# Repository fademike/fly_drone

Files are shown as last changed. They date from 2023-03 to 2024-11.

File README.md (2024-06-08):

# fly_drone

My example drone. (in development)

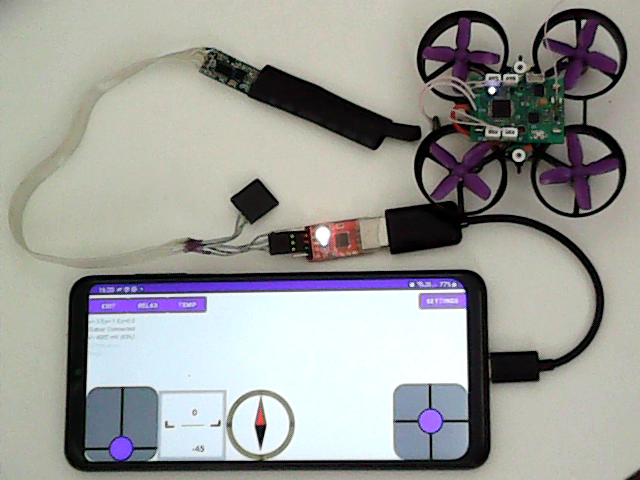
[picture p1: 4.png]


How to connect:
Android phone (AppFlyControl) <-> usb-uart(example: cp2102) <-> uart->rf (STM8S003_AND_SI4463) <-> fly_drone
<br>
or:
<br>
Android phone (QGroundControl or AppFlyControl) <-wifi-> Linux PC (flyLinuxServer) <-> uart->rf (STM8S003_AND_SI4463) <-> fly_drone

on board:
- DC-DC for 2,3,..S battery operation. To operate on a 1S battery, it is necessary to replace the components to turn off the DC-DC.
- RF SI4463 433MHz radio transceiver. when changing the frequency, you can to change components and programmatically set a different frequency.
- imu mpu6050
- 4pcs 3-pin connector for servo motor/ESC (IMP 1-2 ms) for 4pcs brushed motors need to set mosfet or esc for brushed motors.
- i2c connector, for example: for VL53L0X
- connector for debugging by swdio/uart

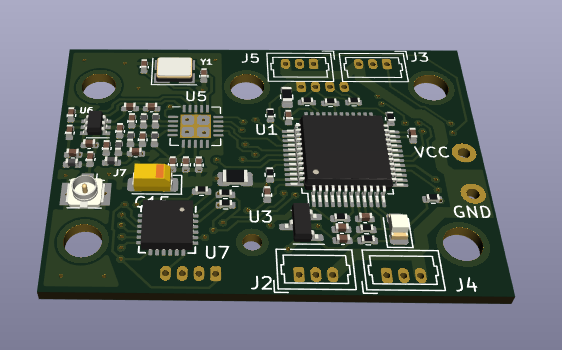
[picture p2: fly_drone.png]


For connect brushed motors with esc or servo motor, you can use convertor on attiny13a. example: kicad->tiny_2nmosfet.
For connect 4pcs brushed motors, you can use n-mosfet on every channel.

<br>
Code:
<br>
bootloader (update firmware via RF by FlyLinuxServer)<br>
fly_drone<br>
- mavlink protocol:<br>
-- params list settings(PID, mux chan, motor settings, orientation)<br>
-- RC_CHANNELS<br>
-- COMMAND_LONG - ARM_DISARM/CALIBRATION/REBOOT<br>
-- MSG_STATUSTEXT - logs<br>
- imu, rf, vl53l0x<br>
- acc and gyro calibrate<br>
- for save params and acc calibrate on flash, need to change "flash_params"<br>
- it is compatible with qgroungcontrol (tested on android)<br>
<br>
And in repository:<br>
kicad:<br>
- ESC_atmega8 - esc for brashless motor. (need to changed frequency by fuses)<br>
- stm32f103_Fly.. - fly_drone project<br>
- tiny_2nmosfet - esc for connection 4 brashed motors(independent 4 in, 4 out)<br>
<br>
video fly_drone.mpg in video repository

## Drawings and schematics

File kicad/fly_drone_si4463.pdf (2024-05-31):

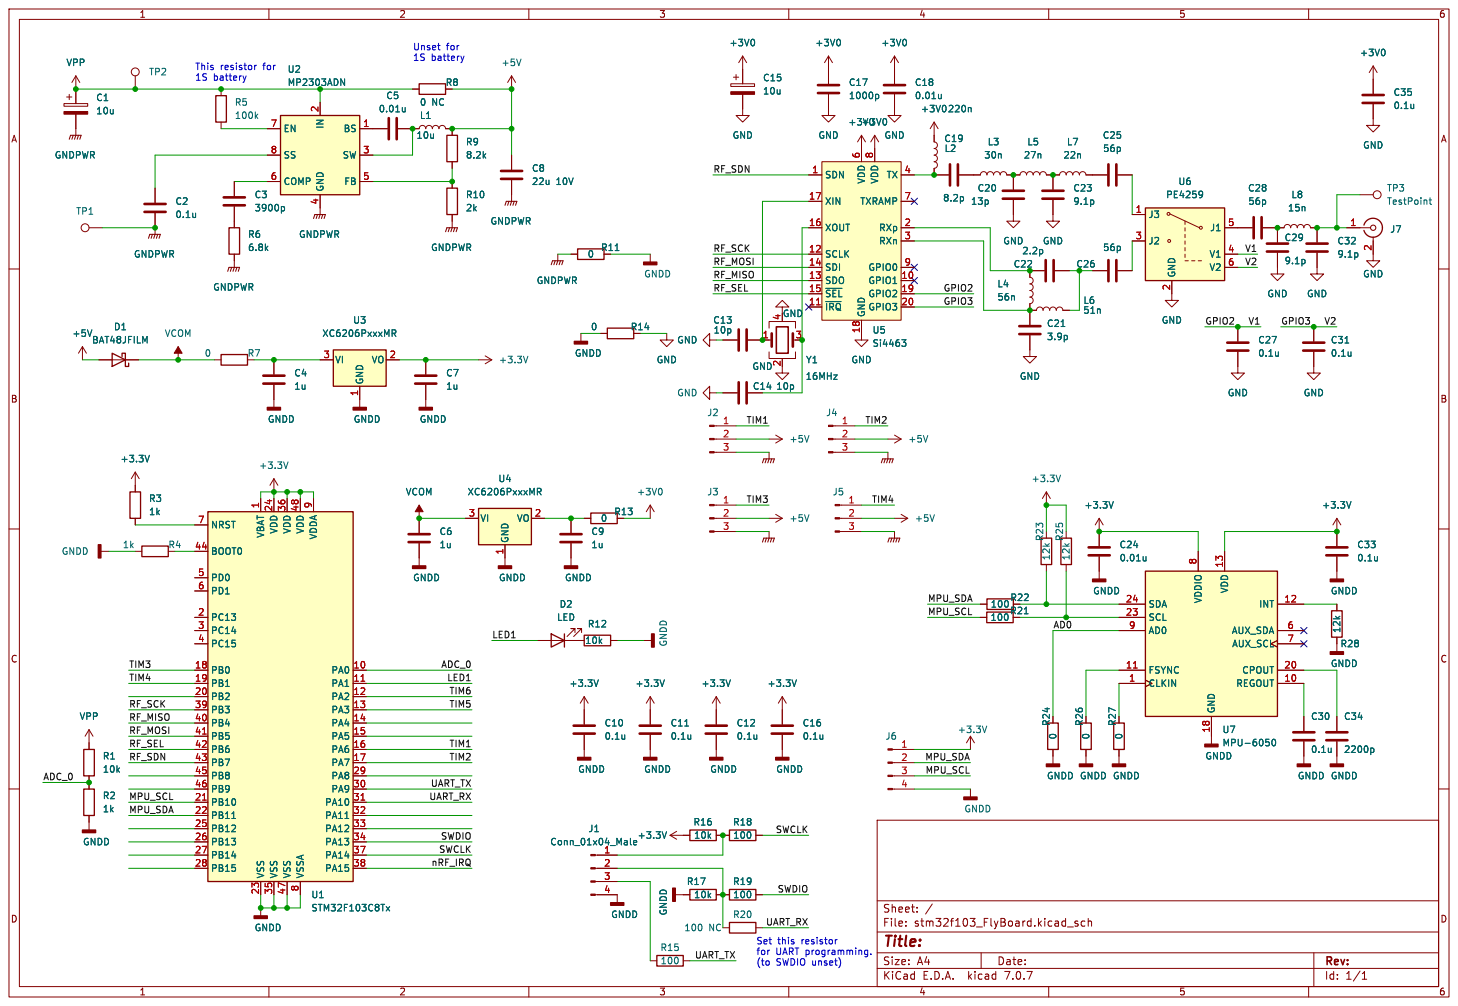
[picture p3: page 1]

4 FB 5 COMP 6 EN 7 SS 8 U2 MP2303ADN

4 FB 5 COMP 6 EN 7 SS 8 R6 GNDPWR

1 PA0 10 PA1 11 PA2 12 PA3 13 PA4 14 PA5 15 PA6 16 PA7 17 PB0 18 PB1 19 PC13 2 PB2 20 PB10 21 PB11 22 VSS 23 VDD 24 PB12 25 PB13 26 PB14 27 PB15 28 PA8 29 PC14 3 PA9 30 PA10 31 PA11 32 PA12 33 PA13 34 VSS 35 VDD 36 PA14 37 PA15 38 PB3 39 PC15 4 PB4 40 PB5 41 PB6 42 PB7 43 BOOT0 44 PB8 45 PB9 46 VSS 47 VDD 48 PD0 5 PD1 6 NRST 7 VSSA

Id: 1/1 Title: File: stm32f103_FlyBoard.kicad_sch Sheet: / GNDD

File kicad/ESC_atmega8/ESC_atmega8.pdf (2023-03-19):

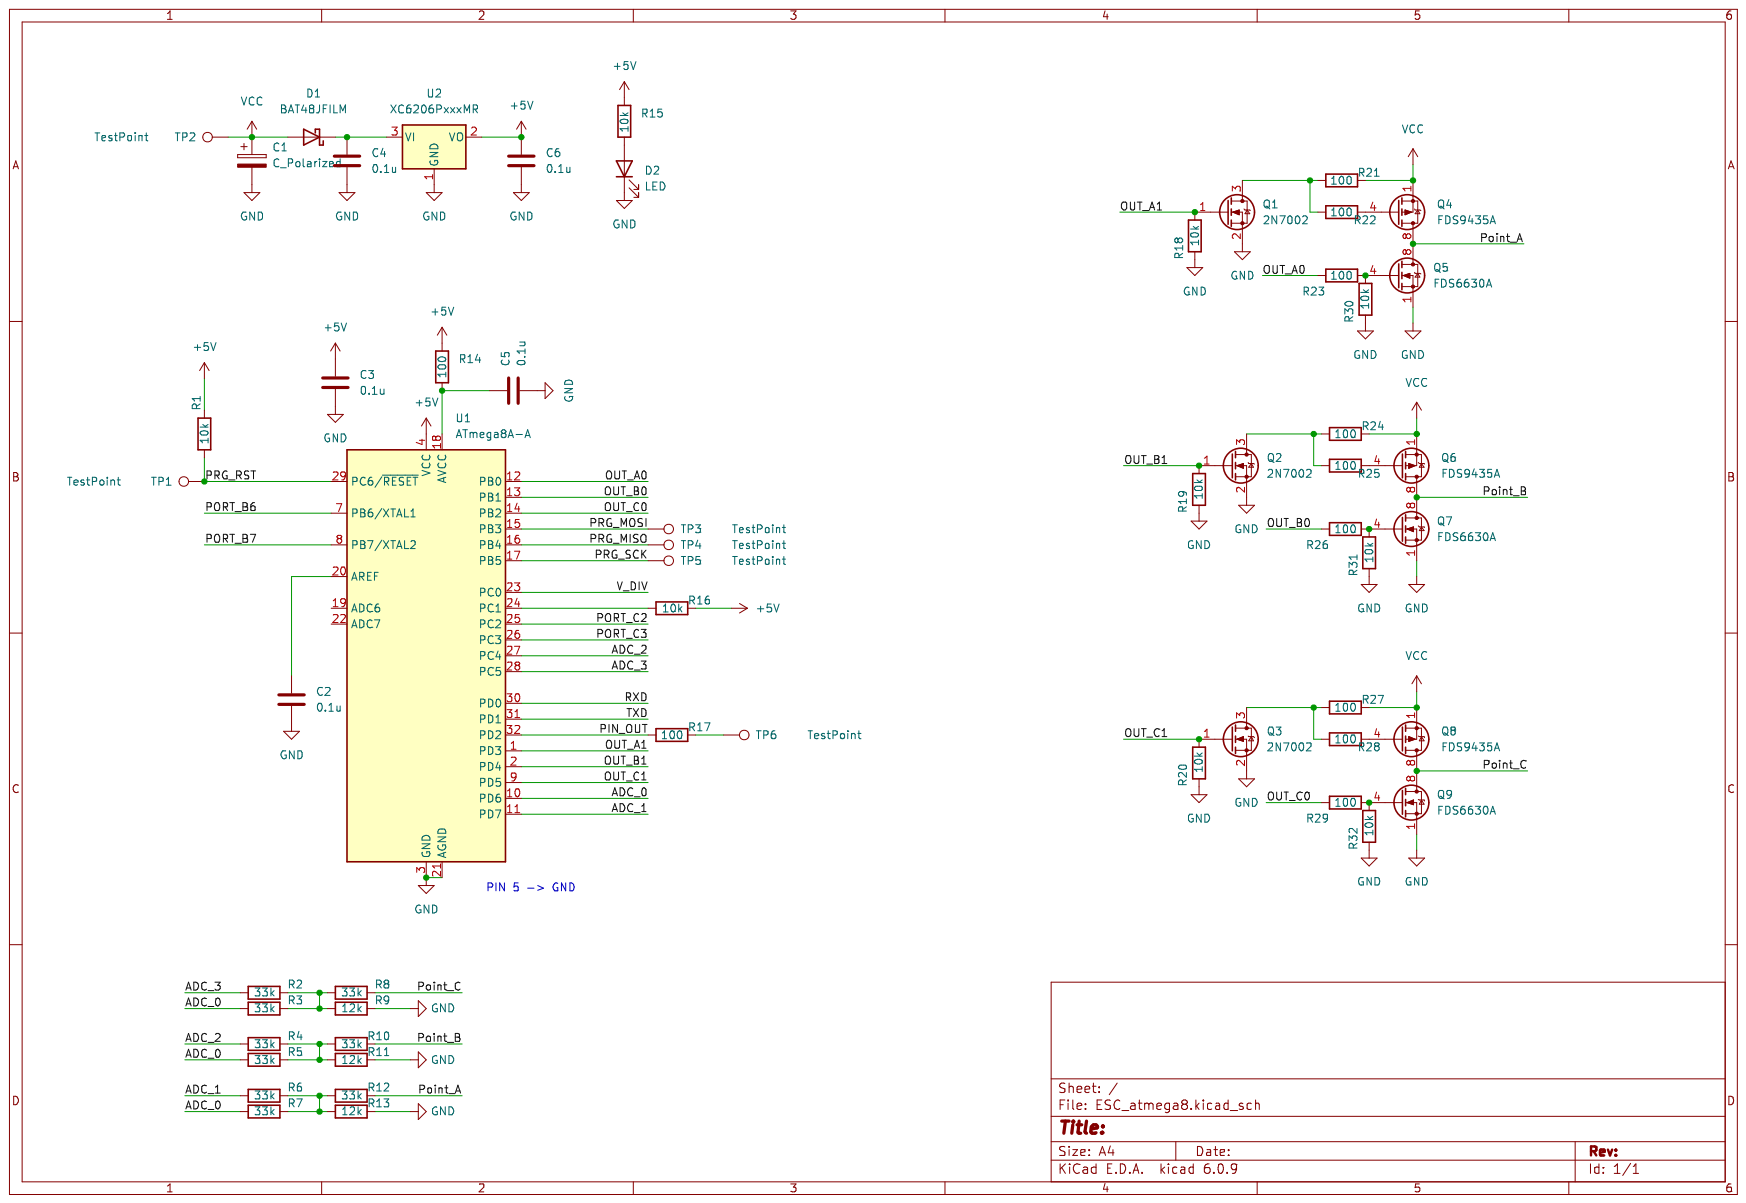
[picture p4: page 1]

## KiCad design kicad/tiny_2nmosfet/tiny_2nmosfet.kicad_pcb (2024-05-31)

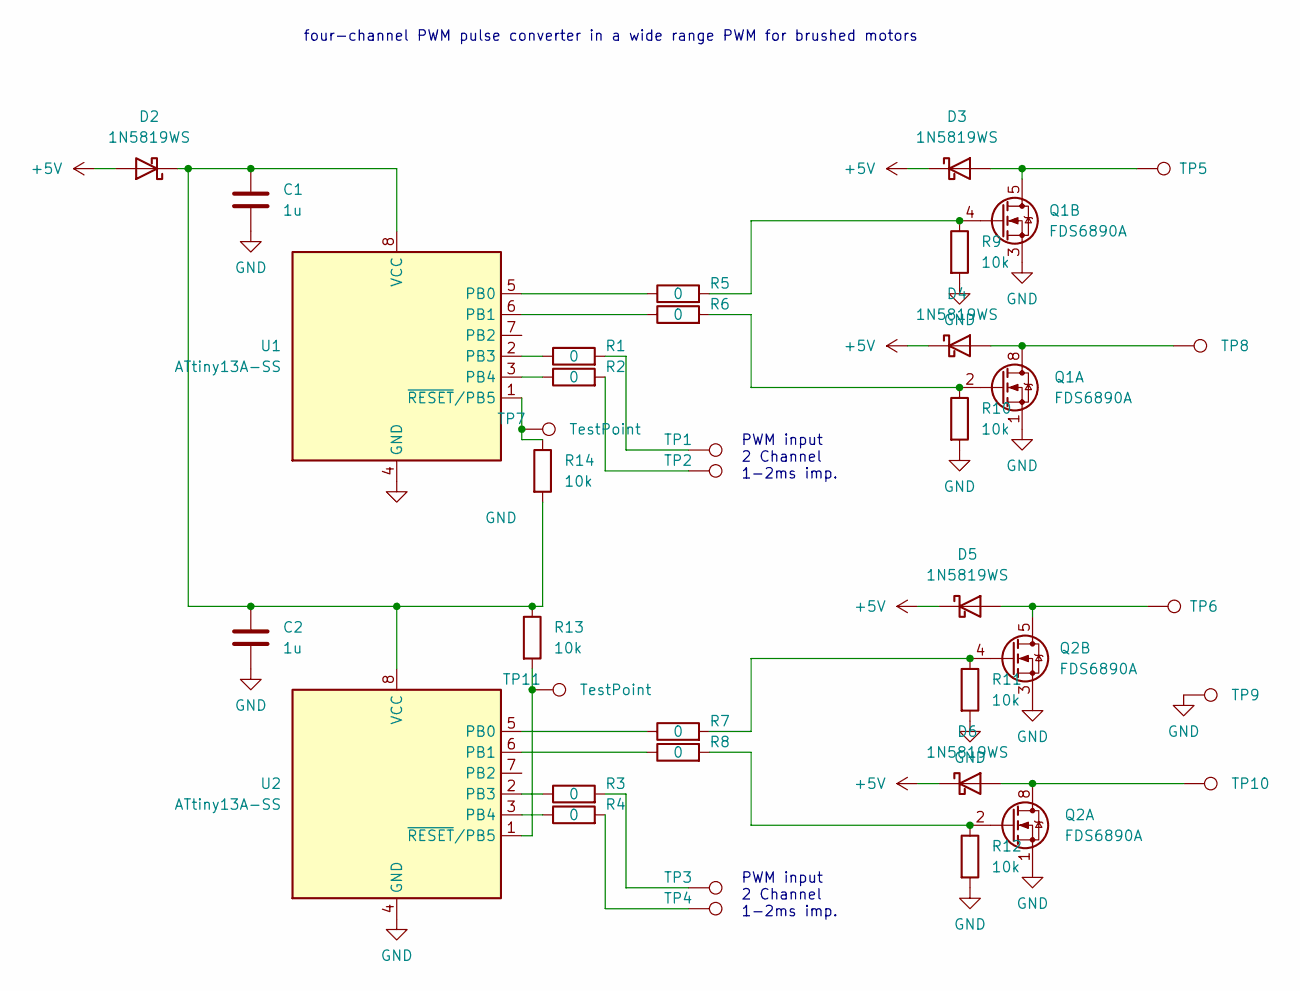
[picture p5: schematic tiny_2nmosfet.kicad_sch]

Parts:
C1, C2: 1u; C_0603_1608Metric
D2, D3, D4, D5, D6: 1N5819WS; D_SOD-323
Q1, Q2: FDS6890A; SOIC-8_3.9x4.9mm_P1.27mm
R1, R2, R3, R4, R5, R6, R7, R8: 0; R_0603_1608Metric
R9, R10, R11, R12, R13, R14: 10k; R_0603_1608Metric
TP1, TP2, TP3, TP4, TP5, TP6, TP7, TP8, TP9, TP10, TP11: TestPoint; PinHeader_1x01_P2.54mm_Vertical
U1, U2: ATtiny13A-SS; SOIC-8_3.9x4.9mm_P1.27mm

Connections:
+5V: D2.2 (A), D3.1 (K), D4.1 (K), D5.1 (K), D6.1 (K)
GND: C1.2, C2.2, Q1.1 (S1), Q1.3 (S2), Q2.1 (S1), Q2.3 (S2), R9.2, R10.2, R11.2, R12.2, TP9.1, U1.4 (GND), U2.4 (GND)
unnamed: C1.1, C2.1, D2.1 (K), R13.1, R14.2, U1.8 (VCC), U2.8 (VCC)
unnamed: D3.2 (A), Q1.5 (D2), Q1.6 (D2), TP5.1
unnamed: D4.2 (A), Q1.7 (D1), Q1.8 (D1), TP8.1
unnamed: D5.2 (A), Q2.5 (D2), Q2.6 (D2), TP6.1
unnamed: D6.2 (A), Q2.7 (D1), Q2.8 (D1), TP10.1
unnamed: Q1.2 (G1), R6.2, R10.1
unnamed: Q1.4 (G2), R5.2, R9.1
unnamed: Q2.2 (G1), R8.2, R12.1
unnamed: Q2.4 (G2), R7.2, R11.1
unnamed: R1.2, TP1.1
unnamed: R2.2, TP2.1
unnamed: R3.2, TP3.1
unnamed: R4.2, TP4.1
unnamed: R5.1, U1.5 (PB0)
unnamed: R6.1, U1.6 (PB1)
unnamed: R1.1, U1.2 (PB3)
unnamed: R2.1, U1.3 (PB4)
unnamed: R14.1, TP7.1, U1.1 (~RESET/PB5)
unnamed: R7.1, U2.5 (PB0)
unnamed: R8.1, U2.6 (PB1)
unnamed: R3.1, U2.2 (PB3)
unnamed: R4.1, U2.3 (PB4)
unnamed: R13.2, TP11.1, U2.1 (~RESET/PB5)

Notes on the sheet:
PWM input 2 Channel 1-2ms imp.
four-channel PWM pulse converter in a wide range PWM for brushed motors

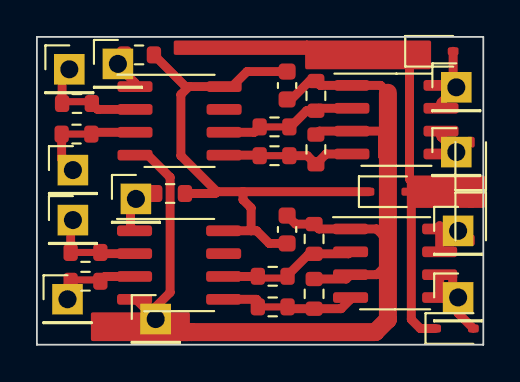
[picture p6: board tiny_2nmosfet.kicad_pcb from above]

Board: 2 copper layers, 24.8 x 17.1 mm, 36 parts (0 on the bottom side), 25 nets.

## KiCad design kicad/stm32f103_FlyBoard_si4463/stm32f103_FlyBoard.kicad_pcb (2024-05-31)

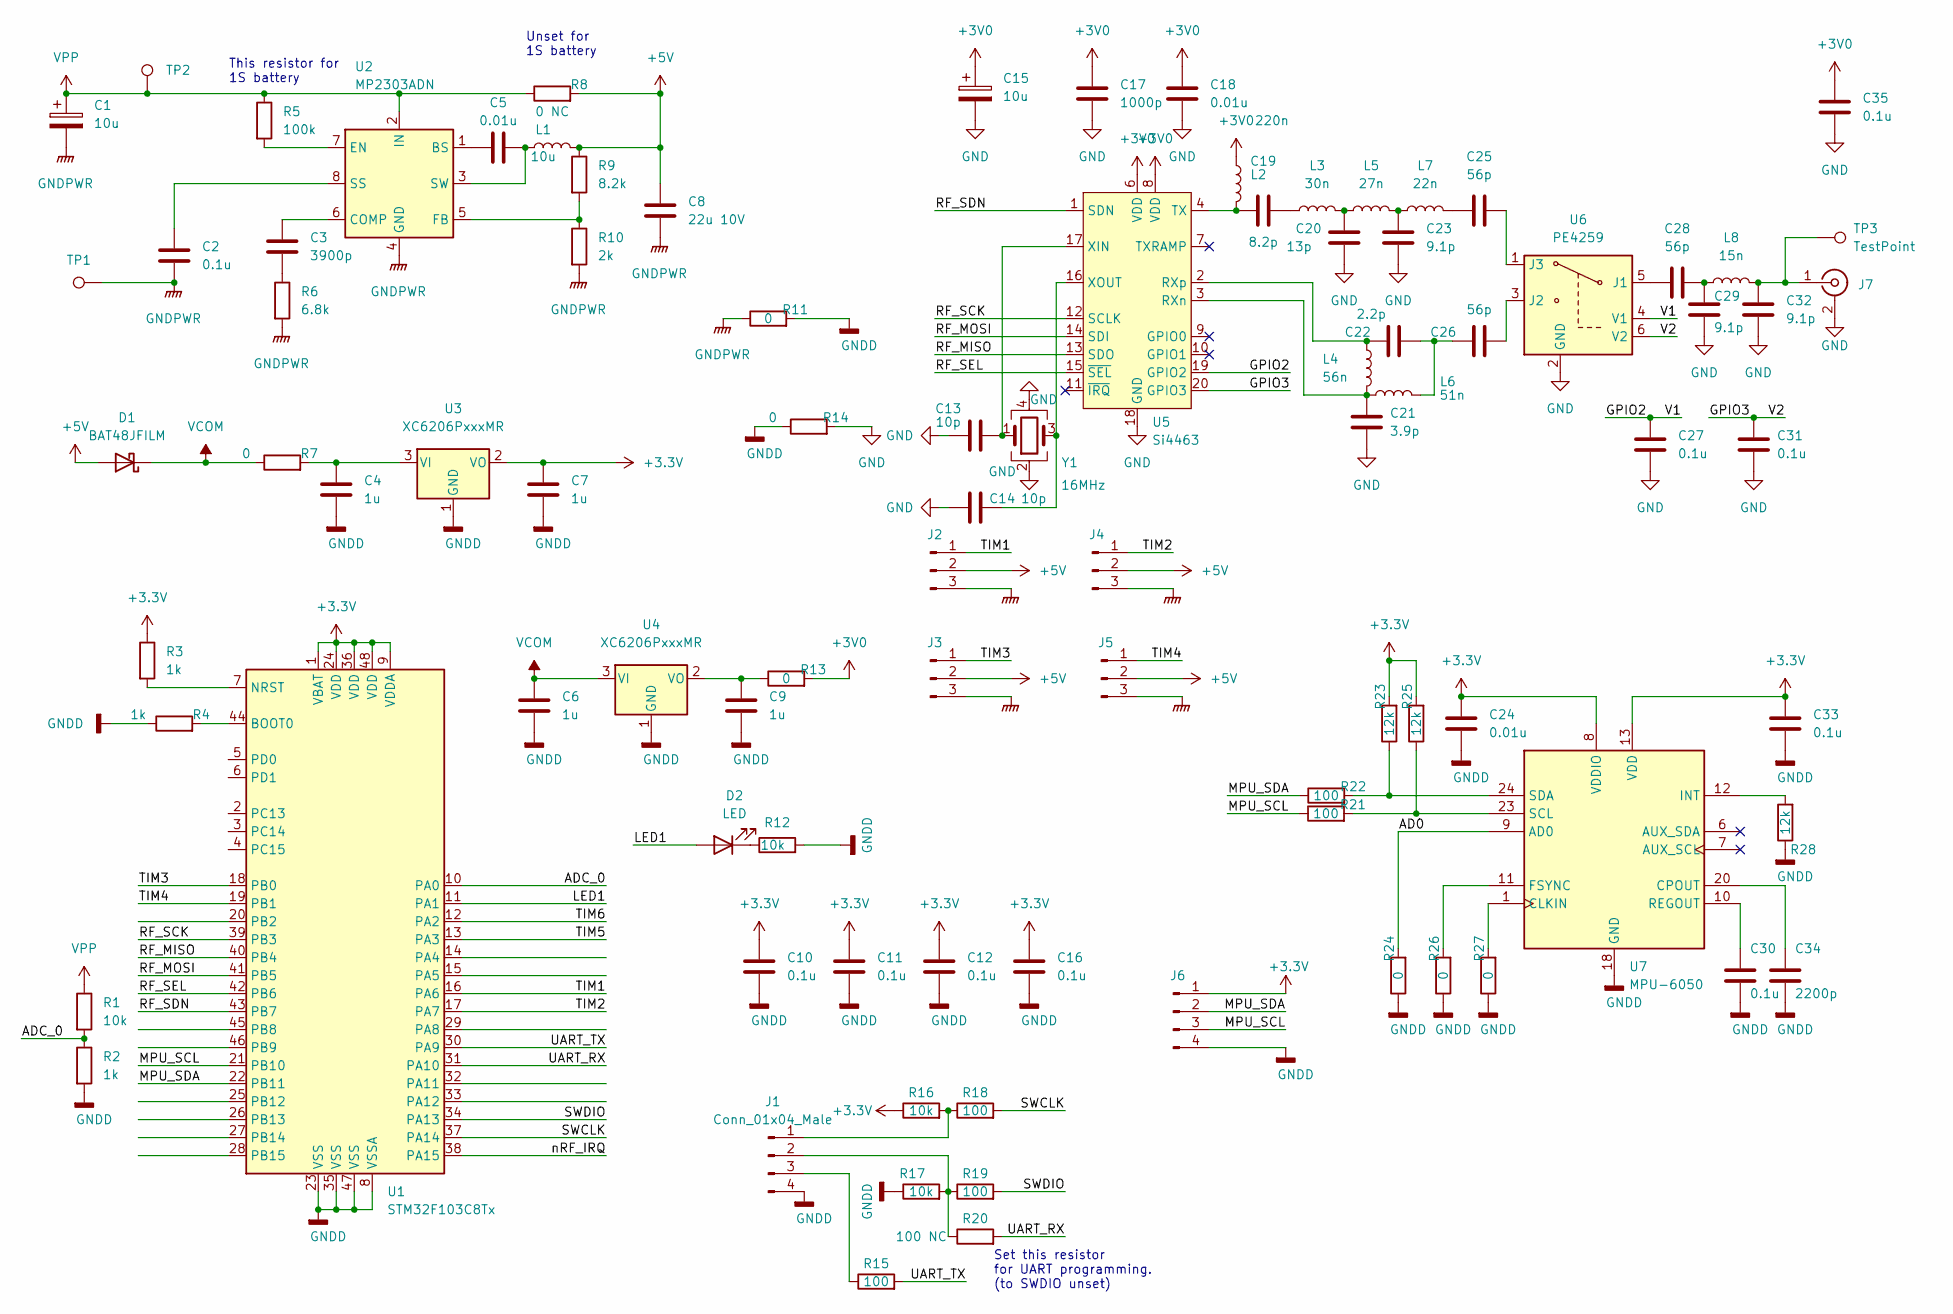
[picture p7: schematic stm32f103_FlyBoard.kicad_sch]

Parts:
C1: 10u; CP_EIA-3528-21_Kemet-B
C2, C10, C11, C12, C16, C27, C30, C31, C33, C35: 0.1u; C_0402_1005Metric
C3: 3900p; C_0402_1005Metric
C4, C6, C7, C9: 1u; C_0402_1005Metric
C5, C18, C24: 0.01u; C_0402_1005Metric
C8: 22u 10V; C_0805_2012Metric
C13, C14: 10p; C_0402_1005Metric
C15: 10u; CP_EIA-3216-18_Kemet-A
C17: 1000p; C_0402_1005Metric
C19: 8.2p; C_0402_1005Metric
C20: 13p; C_0402_1005Metric
C21: 3.9p; C_0402_1005Metric
C22: 2.2p; C_0402_1005Metric
C23, C29, C32: 9.1p; C_0402_1005Metric
C25, C26, C28: 56p; C_0402_1005Metric
C34: 2200p; C_0402_1005Metric
D1: BAT48JFILM; D_SOD-323
D2: LED; LED_0805_2012Metric
J1, J6: Conn_01x04_Male; Molex_PicoBlade_53047-0410_1x04_P1.25mm_Vertical
J2, J3, J4, J5: Conn_01x03_Male; Molex_PicoBlade_53047-0310_1x03_P1.25mm_Vertical
J7: Conn_Coaxial; U.FL_Hirose_U.FL-R-SMT-1_Vertical
L1: 10u; L_Bourns-SRN6028
L2: 220n; L_0402_1005Metric
L3: 30n; L_0402_1005Metric
L4: 56n; L_0402_1005Metric
L5: 27n; L_0402_1005Metric
L6: 51n; L_0402_1005Metric
L7: 22n; L_0402_1005Metric
L8: 15n; L_0402_1005Metric
R1, R12, R17: 10k; R_0402_1005Metric
R2, R3, R4: 1k; R_0402_1005Metric
R5: 100k; R_0402_1005Metric
R6: 6.8k; R_0402_1005Metric
R7, R11, R13, R14: 0; R_0805_2012Metric
R8: 0 NC; R_0805_2012Metric
R9: 8.2k; R_0402_1005Metric
R10: 2k; R_0402_1005Metric
R15, R18, R19, R21, R22: 100; R_0402_1005Metric
R16: 10k; R_0603_1608Metric
R20: 100 NC; R_0402_1005Metric
R23, R25, R28: 12k; R_0402_1005Metric
R24, R26, R27: 0; R_0402_1005Metric
TP1, TP2, TP3: TestPoint; TestPoint_Pad_D1.0mm
U1: STM32F103C8Tx; LQFP-48_7x7mm_P0.5mm
U2: MP2303ADN; SOIC-8-1EP_3.9x4.9mm_P1.27mm_EP2.62x3.51mm
U3, U4: XC6206PxxxMR; SOT-23
U5: Si4463; QFN-20-1EP_4x4mm_P0.5mm_EP2.6x2.6mm
U6: PE4259; SOT-363_SC-70-6
U7: MPU-6050; InvenSense_QFN-24_4x4mm_P0.5mm
Y1: 16MHz; Crystal_SMD_SeikoEpson_FA238-4Pin_3.2x2.5mm

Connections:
+3.3V: C7.1, C10.1, C11.1, C12.1, C16.1, C24.1, C33.1, J6.1, R3.1, R16.1, R23.2, R25.2, U1.1 (VBAT), U1.9 (VDDA), U1.24 (VDD), U1.36 (VDD), U1.48 (VDD), U3.2 (VO), U7.8 (VDDIO), U7.13 (VDD)
+3V0: C15.1, C17.1, C18.1, C35.1, L2.1, R13.2, U5.6 (VDD), U5.8 (VDD)
+5V: C8.1, D1.2 (A), J2.2, J3.2, J4.2, J5.2, L1.2, R8.2, R9.1
/AD0: R24.2, U7.9 (AD0)
/ADC_0: R1.2, R2.1, U1.10 (PA0)
/GPIO2: C27.2, U5.19 (GPIO2), U6.4 (V1)
/GPIO3: C31.2, U5.20 (GPIO3), U6.6 (V2)
/LED1: D2.2 (A), U1.11 (PA1)
/MPU_SCL: J6.3, R21.1, U1.21 (PB10)
/MPU_SDA: J6.2, R22.1, U1.22 (PB11)
/RF_MISO: U1.40 (PB4), U5.13 (SDO)
/RF_MOSI: U1.41 (PB5), U5.14 (SDI)
/RF_SCK: U1.39 (PB3), U5.12 (SCLK)
/RF_SDN: U1.43 (PB7), U5.1 (SDN)
/RF_SEL: U1.42 (PB6), U5.15 (~SEL)
/SWCLK: R18.2, U1.37 (PA14)
/SWDIO: R19.2, U1.34 (PA13)
/TIM1: J2.1, U1.16 (PA6)
/TIM2: J4.1, U1.17 (PA7)
/TIM3: J3.1, U1.18 (PB0)
/TIM4: J5.1, U1.19 (PB1)
/TIM5: U1.13 (PA3)
/TIM6: U1.12 (PA2)
/UART_RX: R20.2, U1.31 (PA10)
/UART_TX: R15.2, U1.30 (PA9)
/nRF_IRQ: U1.38 (PA15)
GND: C13.1, C14.1, C15.2, C17.2, C18.2, C20.1, C21.1, C23.1, C27.1, C29.1, C31.1, C32.1, C35.2, J7.2 (Ext), R14.2, U5.18 (GND), U5.21 (GND), U6.2 (GND), Y1.2, Y1.4
GNDD: C4.2, C6.2, C7.2, C9.2, C10.2, C11.2, C12.2, C16.2, C24.2, C30.2, C33.2, C34.2, J1.4, J6.4, R2.2, R4.1, R11.2, R12.2, R14.1, R17.1, R24.1, R26.1, R27.1, R28.1, U1.8 (VSSA), U1.23 (VSS), U1.35 (VSS), U1.47 (VSS), U3.1 (GND), U4.1 (GND), U7.18 (GND)
GNDPWR: C1.2, C2.2, C8.2, J2.3, J3.3, J4.3, J5.3, R6.2, R10.2, R11.1, TP1.1, U2.4 (GND)
unnamed: C3.2, R6.1
unnamed: C19.2, L3.1
unnamed: C20.2, L3.2, L5.1
unnamed: C22.2, C26.1, L6.2
unnamed: C23.2, L5.2, L7.1
unnamed: C25.2, L7.2
unnamed: C28.1, C29.2, L8.1
unnamed: D2.1 (K), R12.1
unnamed: J1.1, R16.2, R18.1
unnamed: J1.2, R17.2, R19.1, R20.1
unnamed: J1.3, R15.1
unnamed: C32.2, J7.1 (In), L8.2, TP3.1
unnamed: R4.2, U1.44 (BOOT0)
unnamed: R3.2, U1.7 (NRST)
unnamed: C5.1, U2.1 (BS)
unnamed: C3.1, U2.6 (COMP)
unnamed: R5.2, U2.7 (EN)
unnamed: R9.2, R10.1, U2.5 (FB)
unnamed: C2.1, U2.8 (SS)
unnamed: C5.2, L1.1, U2.3 (SW)
unnamed: C4.1, R7.2, U3.3 (VI)
unnamed: C9.1, R13.1, U4.2 (VO)
unnamed: C21.2, L4.2, L6.1, U5.3 (RXn)
unnamed: C22.1, L4.1, U5.2 (RXp)
unnamed: C19.1, L2.2, U5.4 (TX)
unnamed: C13.2, U5.17 (XIN), Y1.1
unnamed: C14.2, U5.16 (XOUT), Y1.3
unnamed: C28.2, U6.5 (J1)
unnamed: C26.2, U6.3 (J2)
unnamed: C25.1, U6.1 (J3)
unnamed: R27.2, U7.1 (CLKIN)
unnamed: C34.1, U7.20 (CPOUT)
unnamed: R26.2, U7.11 (FSYNC)
unnamed: R28.2, U7.12 (INT)
unnamed: C30.1, U7.10 (REGOUT)
unnamed: R21.2, R25.1, U7.23 (SCL)
unnamed: R22.2, R23.1, U7.24 (SDA)
VCOM: C6.1, D1.1 (K), R7.1, U4.3 (VI)
VPP: C1.1, R1.1, R5.1, R8.1, TP2.1, U2.2 (IN)

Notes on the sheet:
Unset for 1S battery
Set this resistor for UART programming. (to SWDIO unset)
This resistor for 1S battery

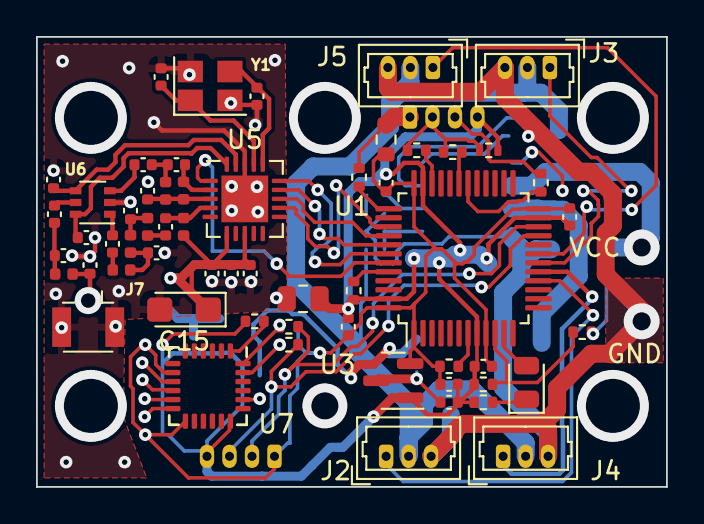
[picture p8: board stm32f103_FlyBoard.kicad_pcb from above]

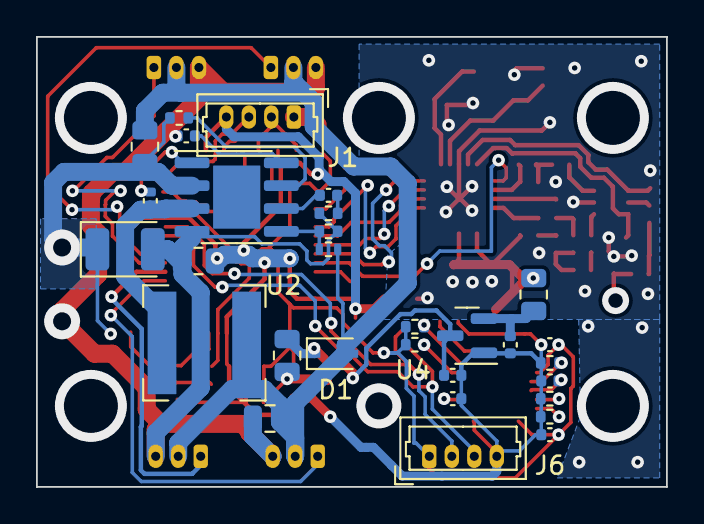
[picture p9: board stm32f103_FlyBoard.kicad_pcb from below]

Board: 2 copper layers, 35.0 x 25.0 mm, 91 parts (30 on the bottom side), 65 nets.

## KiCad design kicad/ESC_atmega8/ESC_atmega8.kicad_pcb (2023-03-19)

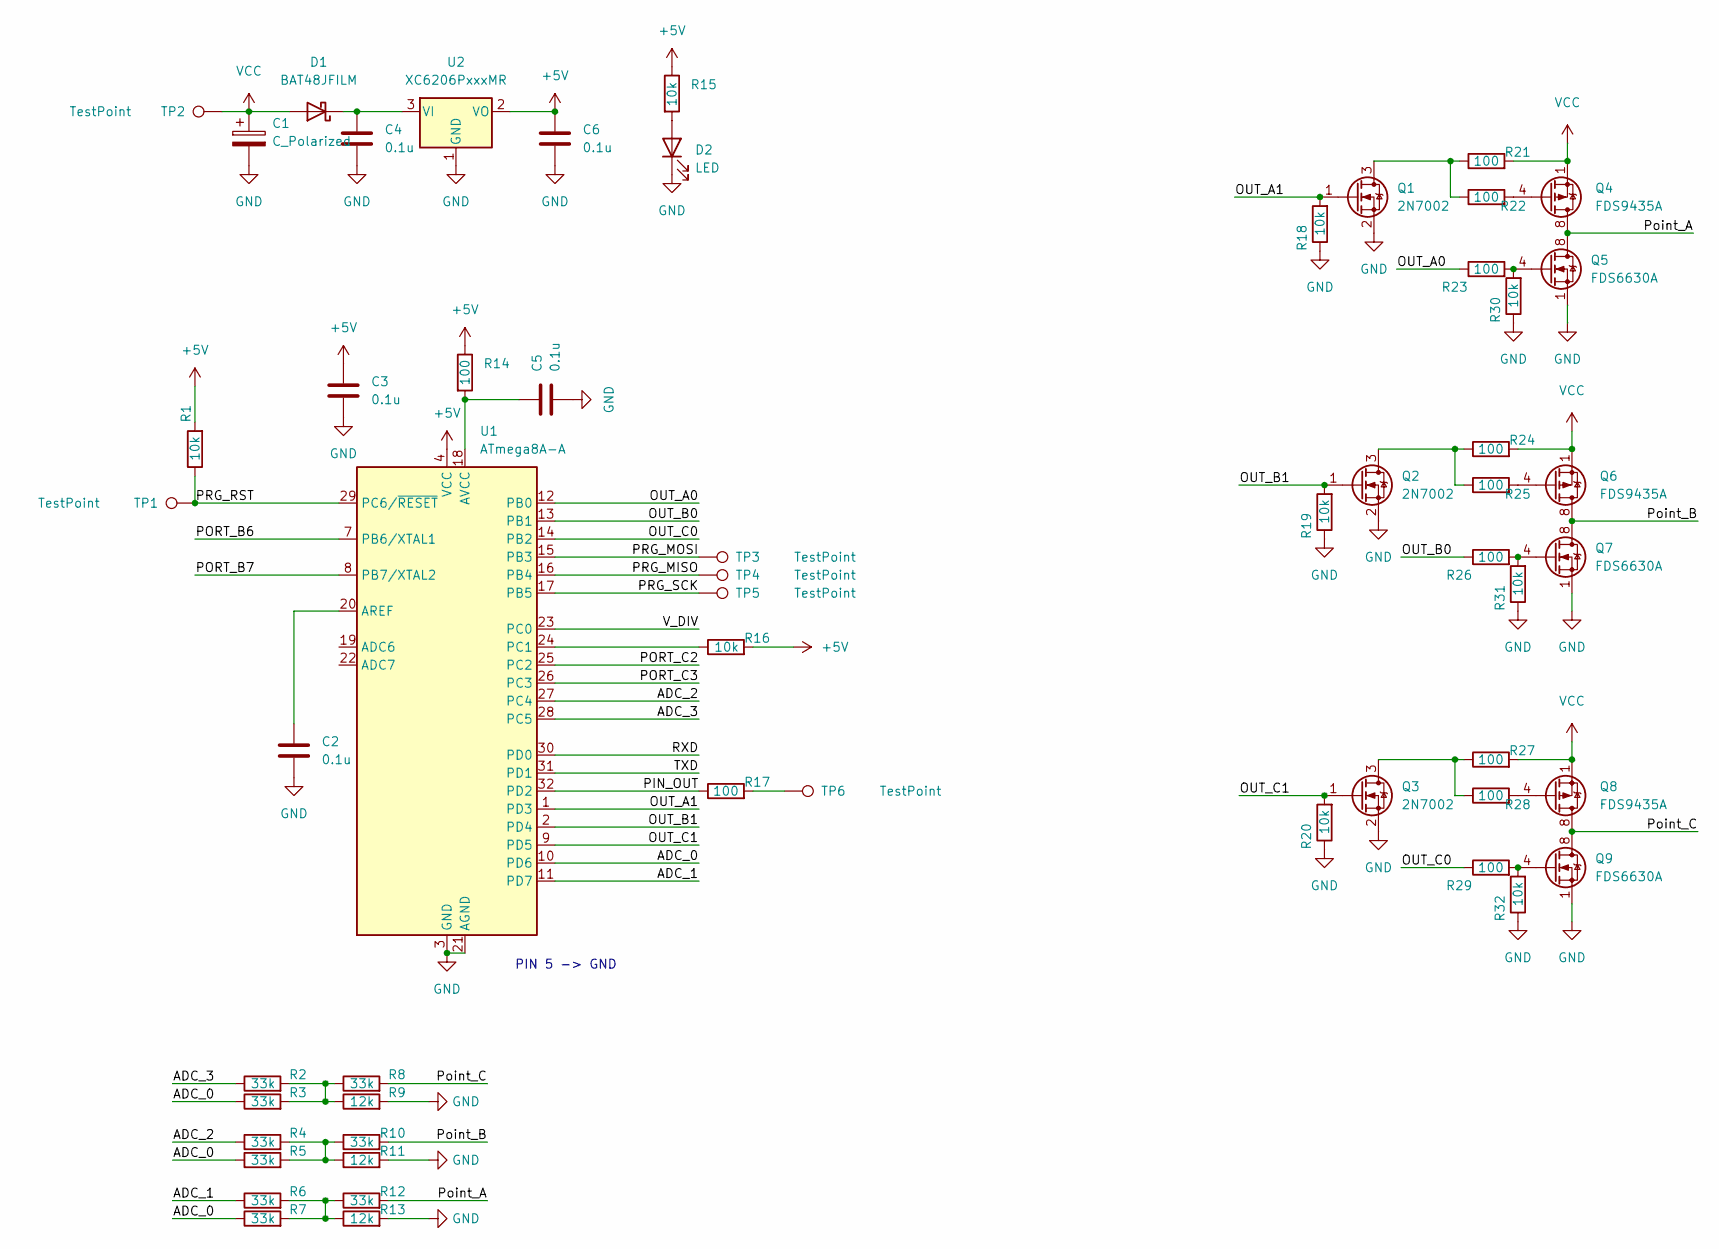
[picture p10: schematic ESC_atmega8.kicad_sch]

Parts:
C1: C_Polarized; CP_EIA-6032-28_Kemet-C
C2, C3, C4, C5, C6: 0.1u; C_0603_1608Metric
D1: BAT48JFILM; D_SOD-323
D2: LED; LED_0805_2012Metric
Q1, Q2, Q3: 2N7002; SOT-23
Q4, Q6, Q8: FDS9435A; SOIC-8_3.9x4.9mm_P1.27mm
Q5, Q7, Q9: FDS6630A; SOIC-8_3.9x4.9mm_P1.27mm
R1, R15, R16, R18, R19, R20, R30, R31, R32: 10k; R_0603_1608Metric
R2, R3, R4, R5, R6, R7, R8, R10, R12: 33k; R_0603_1608Metric
R9, R11, R13: 12k; R_0603_1608Metric
R14, R17, R21, R22, R23, R24, R25, R26, R27, R28, R29: 100; R_0603_1608Metric
TP1, TP2, TP3, TP4, TP5, TP6: TestPoint; TestPoint_Pad_D1.0mm
U1: ATmega8A-A; TQFP-32_7x7mm_P0.8mm
U2: XC6206PxxxMR; SOT-23

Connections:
+5V: C3.1, C6.1, R1.2, R14.1, R15.1, R16.2, U1.4 (VCC), U1.6 (VCC), U2.2 (VO)
/ADC_0: R3.1, R5.1, R7.1, U1.10 (PD6)
/ADC_1: R6.1, U1.11 (PD7)
/ADC_2: R4.1, U1.27 (PC4)
/ADC_3: R2.1, U1.28 (PC5)
/OUT_A0: R23.1, U1.12 (PB0)
/OUT_A1: Q1.1 (G), R18.2, U1.1 (PD3)
/OUT_B0: R26.1, U1.13 (PB1)
/OUT_B1: Q2.1 (G), R19.2, U1.2 (PD4)
/OUT_C0: R29.1, U1.14 (PB2)
/OUT_C1: Q3.1 (G), R20.2, U1.9 (PD5)
/PIN_OUT: R17.1, U1.32 (PD2)
/PORT_B6: U1.7 (PB6/XTAL1)
/PORT_B7: U1.8 (PB7/XTAL2)
/PORT_C2: U1.25 (PC2)
/PORT_C3: U1.26 (PC3)
/PRG_MISO: TP4.1, U1.16 (PB4)
/PRG_MOSI: TP3.1, U1.15 (PB3)
/PRG_RST: R1.1, TP1.1, U1.29 (PC6/~RESET)
/PRG_SCK: TP5.1, U1.17 (PB5)
/Point_A: Q4.5 (D), Q4.6 (D), Q4.7 (D), Q4.8 (D), Q5.5 (D), Q5.6 (D), Q5.7 (D), Q5.8 (D), R12.2
/Point_B: Q6.5 (D), Q6.6 (D), Q6.7 (D), Q6.8 (D), Q7.5 (D), Q7.6 (D), Q7.7 (D), Q7.8 (D), R10.2
/Point_C: Q8.5 (D), Q8.6 (D), Q8.7 (D), Q8.8 (D), Q9.5 (D), Q9.6 (D), Q9.7 (D), Q9.8 (D), R8.2
/RXD: U1.30 (PD0)
/TXD: U1.31 (PD1)
/V_DIV: U1.23 (PC0)
GND: C1.2, C2.2, C3.2, C4.2, C5.2, C6.2, D2.1 (K), Q1.2 (S), Q2.2 (S), Q3.2 (S), Q5.1 (S), Q5.2 (S), Q5.3 (S), Q7.1 (S), Q7.2 (S), Q7.3 (S), Q9.1 (S), Q9.2 (S), Q9.3 (S), R9.2, R11.2, R13.2, R18.1, R19.1, R20.1, R30.1, R31.1, R32.1, U1.3 (GND), U1.5 (GND), U1.21 (AGND), U2.1 (GND)
unnamed: C2.1, U1.20 (AREF)
unnamed: C4.1, D1.1 (K), U2.3 (VI)
unnamed: C5.1, R14.2, U1.18 (AVCC)
unnamed: D2.2 (A), R15.2
unnamed: Q1.3 (D), R21.1, R22.1
unnamed: Q2.3 (D), R24.1, R25.1
unnamed: Q3.3 (D), R27.1, R28.1
unnamed: Q4.4 (G), R22.2
unnamed: Q5.4 (G), R23.2, R30.2
unnamed: Q6.4 (G), R25.2
unnamed: Q7.4 (G), R26.2, R31.2
unnamed: Q8.4 (G), R28.2
unnamed: Q9.4 (G), R29.2, R32.2
unnamed: R2.2, R3.2, R8.1, R9.1
unnamed: R4.2, R5.2, R10.1, R11.1
unnamed: R6.2, R7.2, R12.1, R13.1
unnamed: R16.1, U1.24 (PC1)
unnamed: R17.2, TP6.1
VCC: C1.1, D1.2 (A), Q4.1 (S), Q4.2 (S), Q4.3 (S), Q6.1 (S), Q6.2 (S), Q6.3 (S), Q8.1 (S), Q8.2 (S), Q8.3 (S), R21.2, R24.2, R27.2, TP2.1

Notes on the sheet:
PIN 5 -> GND

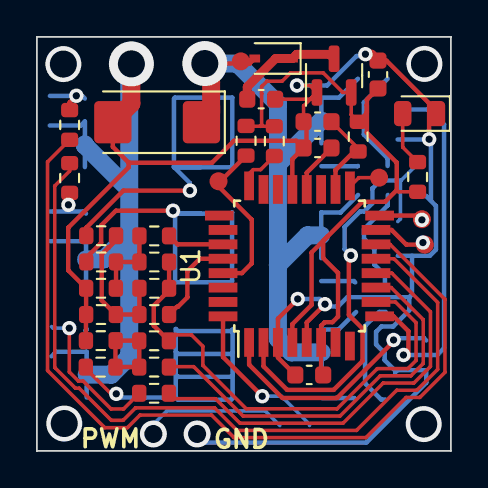
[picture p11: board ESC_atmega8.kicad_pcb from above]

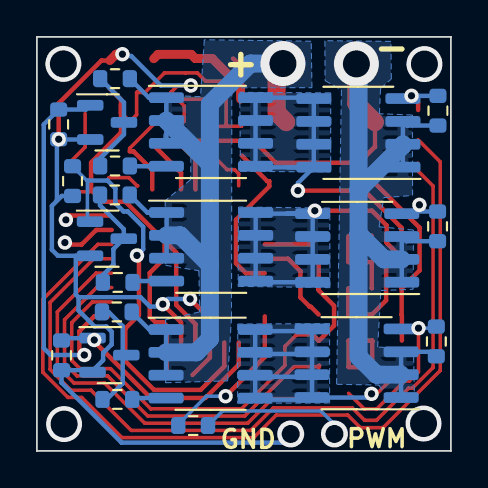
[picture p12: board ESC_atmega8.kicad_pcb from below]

Board: 2 copper layers, 23.0 x 23.0 mm, 57 parts (23 on the bottom side), 39 nets.

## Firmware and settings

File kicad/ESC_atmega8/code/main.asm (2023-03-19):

;**** **** **** **** ****
;
; BLHeli program for controlling brushless motors in helicopters and multirotors
;
; Copyright 2011, 2012 Steffen Skaug
; This program is distributed under the terms of the GNU General Public License
;
; This file is part of BLHeli.
;
; BLHeli is free software: you can redistribute it and/or modify
; it under the terms of the GNU General Public License as published by
; the Free Software Foundation, either version 3 of the License, or
; (at your option) any later version.
;
; BLHeli is distributed in the hope that it will be useful,
; but WITHOUT ANY WARRANTY; without even the implied warranty of
; MERCHANTABILITY or FITNESS FOR A PARTICULAR PURPOSE.  See the
; GNU General Public License for more details.
;
; You should have received a copy of the GNU General Public License
; along with BLHeli.  If not, see <http://www.gnu.org/licenses/>.
;
;**** **** **** **** ****
;
; The software was initially designed for use with Eflite mCP X, but is now adapted to copters/planes in general
;
; The software was inspired by and started from from Bernard Konze's BLMC: http://home.versanet.de/~bkonze/blc_6a/blc_6a.htm
; And also Simon Kirby's TGY: https://github.com/sim-/tgy
;
; This file is best viewed with tab width set to 5
;
; The input signal can be positive 1kHz, 2kHz, 4kHz, 8kHz or 12kHz PWM (e.g. taken from the "resistor tap" on mCPx)
; And the input signal can be PPM (1-2ms) or OneShot125 (125-250us) at rates up to several hundred Hz.
; The code autodetects the various input modes/frequencies
; The code can also be programmed to accept inverted input signal.
;
; The first lines of the software must be modified according to the chosen environment:
; Uncomment the selected ESC and main/tail/multi mode
; BESC EQU "ESC"_"mode" 						
; 
;**** **** **** **** ****
; Revision history:
; - Rev0.0: Initial revision
; - Rev1.0: Governor functionality added
; - Rev1.1: Increased tail gain to 1.0625. Implemented for tail only
;		  Decreased governor proportional and integral gain by 4
; 		  Fixed bug that caused tail power not always to be max
; - Rev1.2: Governor integral gain should be higher in order to achieve full PWM range
;           Integral gain can be higher, and is increased by 2x. An integral of +-128 can now be added to requested PWM
; - Rev1.3: Governor integral extended to 24bit
;		  Governor proportional gain increased by 2x	
;		  Added slow spoolup/down for governor
;		  Set pwm to 100% (do not turn off nFET) for high values of current pwm
;		  Added support for PPM input (1us to 2us pulse)
;		  Removed USE_COMP_STORED as it was never used
; - Rev2.0  Added measurement of pwm frequency and support for 1kHz, 2kHz, 4kHz and 8kHz
;           Optimized pwm on and off routines
;           Improved mosfet switching in beep routines, to reduce current draw
;           Added support for ICP1 interrupt pin input
;           Added ADC measurement of supply voltage, with limiting of main motor power for low voltage
;           Miscellaneous other changes
; - Rev2.1  Rewritten INT0 routine to be similar to ICP
;           Reduced validation threshold (RCP_VALIDATE)
;           Removed requirement for RCP to go to zero again in tail arming sequence
;           Removed PPM support
; - Rev2.2  Added support for HC 5A 1S ESC with Atmega48V MPU
;           Increased governor proportional gain by 2x
; - Rev3.0  Added functionality for programming from TX
;           Added low voltage limit scaling for 2S and 3S
; - Rev11.2 Copied over from the SiLabs version and adapted to Atmel
;           Now requiring a 16MHz capable MCU for fullspec performance
; - Rev12.0 Added programmable main spoolup time
;           Added programmable temperature protection enable
;           Bidirectional mode stop/start improved. Motor is now stopped before starting
;           Power is limited for very low rpms (when BEMF is low), in order to avoid sync loss 
;           Damped light mode is made more smooth and quiet, particularly at low and high rpms
;           Comparator signal qualification scheme is changed
;           Demag compensation scheme is significantly changed
;           Increased jitter tolerance for PPM frequency measurement
;           Fully damped mode removed, and damped light only supported on damped capable ESCs
;           Default tail mode changed to damped light
;           Miscellaneous other changes
; - Rev12.1 Fixed bug in tail code
;           Improved startup for Atmel
;           Added support for multiple high BEC voltages
;           Added support for RPM output
; - Rev12.2 Improved running smoothness, particularly for damped light
;           Avoiding lockup at full throttle when input signal is noisy
;           Avoiding detection of 1-wire programming signal as valid throttle signal
; - Rev13.0 Removed throttle change rate and damping force parameters
;           Temperature protection default set to off
;           Added support for OneShot125
;           Improved commutation timing accuracy
; - Rev13.1 Removed startup ramp for MULTI
;           Improved startup for some odd ESCs
; - Rev13.2 Still tweaking startup to make it more reliable and faster for all ESC/motor combos
;           Increased deadband for bidirectional operation
;           Relaxed signal detection criteria
;           Miscellaneous other changes
; - Rev14.0 Improved running at high RPMs and increased max RPM limit
;           Improved reliability of 3D (bidirectional) mode and startup
;           Avoid being locked in bootloader (implemented in Suite 13202)
;           Smoother running and greatly reduced step to full power in damped light mode
;           Removed low voltage limiting for MULTI
;           Added pwm dither parameter
;           Added setting for enable/disable of low RPM power protection
;           Added setting for enable/disable of PWM input
;           Better AFW and damping for some ESCs (that have a slow high side driver)
;           Miscellaneous other changes
; - Rev14.1 Fixed max throttle calibration bug (for non-oneshot)
;           Fixed some closed loop mode bugs
;           Relaxed signal jitter requirement for looptimes below 1000
;           Added skipping of damping fet switching near max power, for improved high end throttle linearity, using the concept of SimonK
;           Improved sync hold at high rpms
; - Rev14.2 Improved quality of comparator reading, giving better bemf detection (for improved startup amongst others)
;           Removed mechanism where some ESCs could reset upon starting motor (due to ADC being read)
;           Added stalled motor shutoff after about 10 seconds (for tail and multi code with PPM input)
;           Greatly increased maximum rpm limit, and added rpm limiting at 250k erpm
;           Improved bidirectional operation
; - Rev14.3 Moved reset vector to be just before the settings segment, in order to better recover from partially failed flashing operation
;           Shortened stall detect time to about 5sec, and prevented going into tx programming after a stall
;           Optimizations of software timing and running reliability
; - Rev14.4 Improved startup, particularly for larger motors
;           Improved running at very high rpms
;           Made damped light default for MULTI on ESCs that support it
;           Miscellaneous other changes
; - Rev14.5 Longer between beacon beeps (to reduce motor heating), and now again beeping on two motor phases
;           Implemented programmable brake on zero throttle
;           Slightly modified throttle calibration
;           Improved startup, particularly for small motors
;           Improved smoothness
; - Rev14.6 Fixed bug that caused tail motor not to stop
;           Fixed bug that caused brake not to work for low side pwm ESCs
;           Fixed bug where noisy input signal could cause loss of sync
;           Made low rpm power limiting programmable through the startup power parameter
; - Rev14.7 Beeps can be turned off by programming beep strength to 1
;           Throttle cal difference is checked to be above required minimum before storing. Throttle cal max is not stored until successful min throttle cal
;           In order to have a good code for fixed wing planes, that has low voltage limiting, a main code spoolup time setting of 0 is made fast
;           Some small changes for improved sync hold
; - Rev14.8 No change, just created to stay in sync with SiLabs code
; - Rev14.9 Improved bidirectional mode for high input signal rates
;
;
;**** **** **** **** ****
; 8K Bytes of In-System Self-Programmable Flash
; 1K Bytes Internal SRAM
; 512 Bytes Internal EEPROM
; 16MHz clock
;
;**** **** **** **** **** 
; Timer 0 (500ns counts) always counts up and is used for
; - RC pulse timeout and skip counts
; Timer 1 (500ns counts) always counts up and is used for
; - RC pulse measurement (via external interrupt 0 or input capture pin)
; - Commutation timing (via output compare register A interrupt)
; Timer 2 (500ns counts) always counts up and is used for
; - PWM generation
;
;**** **** **** **** ****
; Interrupt handling
; The Atmega8 disables all interrupts when entering an interrupt routine,
; The code reenables interrupts in some interrupt routines, in order to nest pwm interrupts
; - Interrupts are disabled during beeps, to avoid audible interference from interrupts
; - RC pulse interrupts are periodically disabled in order to reduce interference with pwm interrupts.
;
;**** **** **** **** ****
; Motor control:
; - Brushless motor control with 6 states for each electrical 360 degrees
; - An advance timing of 0deg has zero cross 30deg after one commutation and 30deg before the next
; - Timing advance in this implementation is set to 15deg nominally
; - "Damped" commutation schemes are available, where more than one pfet is on when pwm is off. This will absorb energy from bemf and make step settling more damped.
; Motor sequence starting from zero crossing:
; - Timer wait: Wt_Comm			15deg	; Time to wait from zero cross to actual commutation
; - Timer wait: Wt_Advance		15deg	; Time to wait for timing advance. Nominal commutation point is after this
; - Timer wait: Wt_Zc_Scan		7.5deg	; Time to wait before looking for zero cross
; - Scan for zero cross			22.5deg	, Nominal, with some motor variations
;
; Motor startup:
; There is a startup phase and an initial run phase, before normal bemf commutation run begins.
;
;**** **** **** **** ****
; Select the ESC and mode to use (or unselect all for use with external batch compile file);
;#define BLUESERIES_12A_MAIN 
;#define BLUESERIES_12A_TAIL
;#define BLUESERIES_12A_MULTI 
;#define BLUESERIES_20A_MAIN
;#define BLUESERIES_20A_TAIL
;#define BLUESERIES_20A_MULTI
;#define BLUESERIES_30A_MAIN
;#define BLUESERIES_30A_TAIL
;#define BLUESERIES_30A_MULTI 
;#define BLUESERIES_40A_MAIN
;#define BLUESERIES_40A_TAIL
;#define BLUESERIES_40A_MULTI
;#define BLUESERIES_60A_MAIN
;#define BLUESERIES_60A_TAIL
;#define BLUESERIES_60A_MULTI
;#define BLUESERIES_70A_MAIN
;#define BLUESERIES_70A_TAIL
;#define BLUESERIES_70A_MULTI
;#define HK_UBEC_6A_MAIN
;#define HK_UBEC_6A_TAIL
;#define HK_UBEC_6A_MULTI
;#define HK_UBEC_10A_MAIN
;#define HK_UBEC_10A_TAIL
;#define HK_UBEC_10A_MULTI
;#define HK_UBEC_20A_MAIN
;#define HK_UBEC_20A_TAIL
;#define HK_UBEC_20A_MULTI
;#define HK_UBEC_30A_MAIN
;#define HK_UBEC_30A_TAIL
;#define HK_UBEC_30A_MULTI
;#define HK_UBEC_40A_MAIN
;#define HK_UBEC_40A_TAIL
;#define HK_UBEC_40A_MULTI
;#define SUPERSIMPLE_18A_MAIN
;#define SUPERSIMPLE_18A_TAIL
;#define SUPERSIMPLE_18A_MULTI
;#define SUPERSIMPLE_20A_MAIN
;#define SUPERSIMPLE_20A_TAIL
;#define SUPERSIMPLE_20A_MULTI
;#define SUPERSIMPLE_30A_MAIN
;#define SUPERSIMPLE_30A_TAIL
;#define SUPERSIMPLE_30A_MULTI
;#define SUPERSIMPLE_40A_MAIN
;#define SUPERSIMPLE_40A_TAIL
;#define SUPERSIMPLE_40A_MULTI
;#define MULTISTAR_10Av2_MAIN			
;#define MULTISTAR_10Av2_TAIL
;#define MULTISTAR_10Av2_MULTI
;#define MULTISTAR_15A_MAIN			; Inverted input
;#define MULTISTAR_15A_TAIL
;#define MULTISTAR_15A_MULTI
;#define MULTISTAR_20A_MAIN			; Inverted input
;#define MULTISTAR_20A_TAIL
;#define MULTISTAR_20A_MULTI
;#define MULTISTAR_20A_NFET_MAIN		; Inverted input
;#define MULTISTAR_20A_NFET_TAIL
;#define MULTISTAR_20A_NFET_MULTI
;#define MULTISTAR_20Av2_MAIN			
;#define MULTISTAR_20Av2_TAIL
;#define MULTISTAR_20Av2_MULTI
;#define MULTISTAR_30A_MAIN			; Inverted input
;#define MULTISTAR_30A_TAIL
;#define MULTISTAR_30A_MULTI
;#define MULTISTAR_40Av2_MAIN			
;#define MULTISTAR_40Av2_TAIL
;#define MULTISTAR_40Av2_MULTI
;#define MULTISTAR_45A_MAIN			; Inverted input
;#define MULTISTAR_45A_TAIL
;#define MULTISTAR_45A_MULTI
;#define MYSTERY_12A_MAIN			
;#define MYSTERY_12A_TAIL
;#define MYSTERY_12A_MULTI 
;#define MYSTERY_30A_MAIN			
;#define MYSTERY_30A_TAIL
;#define MYSTERY_30A_MULTI
;#define MYSTERY_40A_MAIN			
;#define MYSTERY_40A_TAIL
;#define MYSTERY_40A_MULTI
;#define SUNRISE_HIMULTI_20A_MAIN		; Inverted input
;#define SUNRISE_HIMULTI_20A_TAIL
;#define SUNRISE_HIMULTI_20A_MULTI
;#define SUNRISE_HIMULTI_30A_MAIN		; Inverted input
;#define SUNRISE_HIMULTI_30A_TAIL
;#define SUNRISE_HIMULTI_30A_MULTI
;#define SUNRISE_HIMULTI_40A_MAIN		; Inverted input
;#define SUNRISE_HIMULTI_40A_TAIL
;#define SUNRISE_HIMULTI_40A_MULTI 
;#define RCTIMER_40A_MAIN			
;#define RCTIMER_40A_TAIL
#define RCTIMER_40A_MULTI 
;#define RCTIMER_NFS_30A_MAIN			; ICP1 as input		
;#define RCTIMER_NFS_30A_TAIL
;#define RCTIMER_NFS_30A_MULTI
;#define YEP_7A_MAIN					
;#define YEP_7A_TAIL
;#define YEP_7A_MULTI 
;#define AFRO_12A_MAIN				; ICP1 as input		
;#define AFRO_12A_TAIL
;#define AFRO_12A_MULTI 
;#define AFRO_20A_MAIN				; ICP1 as input		
;#define AFRO_20A_TAIL
;#define AFRO_20A_MULTI
;#define AFRO_20A_HV_MAIN			; ICP1 as input		
;#define AFRO_20A_HV_TAIL
;#define AFRO_20A_HV_MULTI
;#define AFRO_30A_MAIN				; ICP1 as input		
;#define AFRO_30A_TAIL
;#define AFRO_30A_MULTI 
;#define SUNRISE_BLHELI_SLIM_20A_MAIN	
;#define SUNRISE_BLHELI_SLIM_20A_TAIL
;#define SUNRISE_BLHELI_SLIM_20A_MULTI
;#define SUNRISE_BLHELI_SLIM_30A_MAIN	
;#define SUNRISE_BLHELI_SLIM_30A_TAIL
;#define SUNRISE_BLHELI_SLIM_30A_MULTI
;#define DYS_SN20A_MAIN				; ICP1 as input		
;#define DYS_SN20A_TAIL
;#define DYS_SN20A_MULTI 
;#define TBS_CUBE_20A_MAIN			; ICP1 as input		
;#define TBS_CUBE_20A_TAIL
;#define TBS_CUBE_20A_MULTI
;#define ZTW_SPIDER_LITE_18Av2_MAIN
;#define ZTW_SPIDER_LITE_18Av2_TAIL
;#define ZTW_SPIDER_LITE_18Av2_MULTI
;#define HTIRC_DRAGONFLY_6A_MAIN
;#define HTIRC_DRAGONFLY_6A_TAIL
;#define HTIRC_DRAGONFLY_6A_MULTI 
;#define HTIRC_DRAGONFLY_12A_MAIN
;#define HTIRC_DRAGONFLY_12A_TAIL
;#define HTIRC_DRAGONFLY_12A_MULTI 
;#define HTIRC_DRAGONFLY_20A_MAIN
;#define HTIRC_DRAGONFLY_20A_TAIL
;#define HTIRC_DRAGONFLY_20A_MULTI 
;#define HTIRC_DRAGONFLY_30A_MAIN
;#define HTIRC_DRAGONFLY_30A_TAIL
;#define HTIRC_DRAGONFLY_30A_MULTI 
;#define HTIRC_DRAGONFLY_40A_MAIN
;#define HTIRC_DRAGONFLY_40A_TAIL
;#define HTIRC_DRAGONFLY_40A_MULTI 
;#define TBS_BULLETPROOF_4A_MAIN			; ICP1 as input		
;#define TBS_BULLETPROOF_4A_TAIL
;#define TBS_BULLETPROOF_4A_MULTI
;#define TBS_BULLETPROOF_30A_MAIN			; ICP1 as input		
;#define TBS_BULLETPROOF_30A_TAIL
;#define TBS_BULLETPROOF_30A_MULTI



;**** **** **** **** ****
; ESC selection statements
#if defined(BLUESERIES_12A_MAIN)
.EQU	MODE 	= 	0			; Choose mode. Set to 0 for main motor
.INCLUDE "BlueSeries_12A.inc"		; Select BlueSeries 12A pinout
#endif

#if defined(BLUESERIES_12A_TAIL)
.EQU	MODE 	= 	1			; Choose mode. Set to 1 for tail motor
.INCLUDE "BlueSeries_12A.inc"		; Select BlueSeries 12A pinout
#endif

#if defined(BLUESERIES_12A_MULTI)
.EQU	MODE 	= 	2			; Choose mode. Set to 2 for multirotor
.INCLUDE "BlueSeries_12A.inc"		; Select BlueSeries 12A pinout
#endif

#if defined(BLUESERIES_20A_MAIN)
.EQU	MODE 	= 	0			; Choose mode. Set to 0 for main motor
.INCLUDE "BlueSeries_20A.inc"		; Select BlueSeries 20A pinout
#endif

#if defined(BLUESERIES_20A_TAIL)
.EQU	MODE 	= 	1			; Choose mode. Set to 1 for tail motor
.INCLUDE "BlueSeries_20A.inc"		; Select BlueSeries 20A pinout
#endif

#if defined(BLUESERIES_20A_MULTI)
.EQU	MODE 	= 	2			; Choose mode. Set to 2 for multirotor
.INCLUDE "BlueSeries_20A.inc"		; Select BlueSeries 20A pinout
#endif

#if defined(BLUESERIES_30A_MAIN)
.EQU	MODE 	= 	0			; Choose mode. Set to 0 for main motor
.INCLUDE "BlueSeries_30A.inc"		; Select BlueSeries 30A pinout
#endif

#if defined(BLUESERIES_30A_TAIL)
.EQU	MODE 	= 	1			; Choose mode. Set to 1 for tail motor
.INCLUDE "BlueSeries_30A.inc"		; Select BlueSeries 30A pinout
#endif

#if defined(BLUESERIES_30A_MULTI)
.EQU	MODE 	= 	2			; Choose mode. Set to 2 for multirotor
.INCLUDE "BlueSeries_30A.inc"		; Select BlueSeries 30A pinout
#endif

#if defined(BLUESERIES_40A_MAIN)
.EQU	MODE 	= 	0			; Choose mode. Set to 0 for main motor
.INCLUDE "BlueSeries_40A.inc"		; Select BlueSeries 40A pinout
#endif

#if defined(BLUESERIES_40A_TAIL)
.EQU	MODE 	= 	1			; Choose mode. Set to 1 for tail motor
.INCLUDE "BlueSeries_40A.inc"		; Select BlueSeries 40A pinout
#endif

#if defined(BLUESERIES_40A_MULTI)
.EQU	MODE 	= 	2			; Choose mode. Set to 2 for multirotor
.INCLUDE "BlueSeries_40A.inc"		; Select BlueSeries 40A pinout
#endif

#if defined(BLUESERIES_60A_MAIN)
.EQU	MODE 	= 	0			; Choose mode. Set to 0 for main motor
.INCLUDE "BlueSeries_60A.inc"		; Select BlueSeries 60A pinout
#endif

#if defined(BLUESERIES_60A_TAIL)
.EQU	MODE 	= 	1			; Choose mode. Set to 1 for tail motor
.INCLUDE "BlueSeries_60A.inc"		; Select BlueSeries 60A pinout
#endif

#if defined(BLUESERIES_60A_MULTI)
.EQU	MODE 	= 	2			; Choose mode. Set to 2 for multirotor
.INCLUDE "BlueSeries_60A.inc"		; Select BlueSeries 60A pinout
#endif

#if defined(BLUESERIES_70A_MAIN)
.EQU	MODE 	= 	0			; Choose mode. Set to 0 for main motor
.INCLUDE "BlueSeries_70A.inc"		; Select BlueSeries 70A pinout
#endif

#if defined(BLUESERIES_70A_TAIL)
.EQU	MODE 	= 	1			; Choose mode. Set to 1 for tail motor
.INCLUDE "BlueSeries_70A.inc"		; Select BlueSeries 70A pinout
#endif

#if defined(BLUESERIES_70A_MULTI)
.EQU	MODE 	= 	2			; Choose mode. Set to 2 for multirotor
.INCLUDE "BlueSeries_70A.inc"		; Select BlueSeries 70A pinout
#endif

#if defined(HK_UBEC_6A_MAIN)
.EQU	MODE 	= 	0			; Choose mode. Set to 0 for main motor
.INCLUDE "HK_UBEC_6A.inc"		; Select Hobbyking UBEC 6A pinout
#endif

#if defined(HK_UBEC_6A_TAIL)
.EQU	MODE 	= 	1			; Choose mode. Set to 1 for tail motor
.INCLUDE "HK_UBEC_6A.inc"		; Select Hobbyking UBEC 6A pinout
#endif

#if defined(HK_UBEC_6A_MULTI)
.EQU	MODE 	= 	2			; Choose mode. Set to 2 for multirotor
.INCLUDE "HK_UBEC_6A.inc"		; Select Hobbyking UBEC 6A pinout
#endif

#if defined(HK_UBEC_10A_MAIN)
.EQU	MODE 	= 	0			; Choose mode. Set to 0 for main motor
.INCLUDE "HK_UBEC_10A.inc"		; Select Hobbyking UBEC 10A pinout
#endif

#if defined(HK_UBEC_10A_TAIL)
.EQU	MODE 	= 	1			; Choose mode. Set to 1 for tail motor
.INCLUDE "HK_UBEC_10A.inc"		; Select Hobbyking UBEC 10A pinout
#endif

#if defined(HK_UBEC_10A_MULTI)
.EQU	MODE 	= 	2			; Choose mode. Set to 2 for multirotor
.INCLUDE "HK_UBEC_10A.inc"		; Select Hobbyking UBEC 10A pinout
#endif

#if defined(HK_UBEC_20A_MAIN)
.EQU	MODE 	= 	0			; Choose mode. Set to 0 for main motor
.INCLUDE "HK_UBEC_20A.inc"		; Select Hobbyking UBEC 20A pinout
#endif

#if defined(HK_UBEC_20A_TAIL)
.EQU	MODE 	= 	1			; Choose mode. Set to 1 for tail motor
.INCLUDE "HK_UBEC_20A.inc"		; Select Hobbyking UBEC 20A pinout
#endif

#if defined(HK_UBEC_20A_MULTI)
.EQU	MODE 	= 	2			; Choose mode. Set to 2 for multirotor
.INCLUDE "HK_UBEC_20A.inc"		; Select Hobbyking UBEC 20A pinout
#endif

#if defined(HK_UBEC_30A_MAIN)
.EQU	MODE 	= 	0			; Choose mode. Set to 0 for main motor
.INCLUDE "HK_UBEC_30A.inc"		; Select Hobbyking UBEC 30A pinout
#endif

#if defined(HK_UBEC_30A_TAIL)
.EQU	MODE 	= 	1			; Choose mode. Set to 1 for tail motor
.INCLUDE "HK_UBEC_30A.inc"		; Select Hobbyking UBEC 30A pinout
#endif

#if defined(HK_UBEC_30A_MULTI)
.EQU	MODE 	= 	2			; Choose mode. Set to 2 for multirotor
.INCLUDE "HK_UBEC_30A.inc"		; Select Hobbyking UBEC 30A pinout
#endif

#if defined(HK_UBEC_40A_MAIN)
.EQU	MODE 	= 	0			; Choose mode. Set to 0 for main motor
.INCLUDE "HK_UBEC_40A.inc"		; Select Hobbyking UBEC 40A pinout
#endif

#if defined(HK_UBEC_40A_TAIL)
.EQU	MODE 	= 	1			; Choose mode. Set to 1 for tail motor
.INCLUDE "HK_UBEC_40A.inc"		; Select Hobbyking UBEC 40A pinout
#endif

#if defined(HK_UBEC_40A_MULTI)
.EQU	MODE 	= 	2			; Choose mode. Set to 2 for multirotor
.INCLUDE "HK_UBEC_40A.inc"		; Select Hobbyking UBEC 40A pinout
#endif

#if defined(SUPERSIMPLE_18A_MAIN)
.EQU	MODE 	= 	0			; Choose mode. Set to 0 for main motor
.INCLUDE "SuperSimple_18A.inc"	; Select SuperSimple 18A pinout
#endif

#if defined(SUPERSIMPLE_18A_TAIL)
.EQU	MODE 	= 	1			; Choose mode. Set to 1 for tail motor
.INCLUDE "SuperSimple_18A.inc"	; Select SuperSimple 18A pinout
#endif

#if defined(SUPERSIMPLE_18A_MULTI)
.EQU	MODE 	= 	2			; Choose mode. Set to 2 for multirotor
.INCLUDE "SuperSimple_18A.inc"	; Select SuperSimple 18A pinout
#endif

#if defined(SUPERSIMPLE_20A_MAIN)
.EQU	MODE 	= 	0			; Choose mode. Set to 0 for main motor
.INCLUDE "SuperSimple_20A.inc"	; Select SuperSimple 20A pinout
#endif

#if defined(SUPERSIMPLE_20A_TAIL)
.EQU	MODE 	= 	1			; Choose mode. Set to 1 for tail motor
.INCLUDE "SuperSimple_20A.inc"	; Select SuperSimple 20A pinout
#endif

#if defined(SUPERSIMPLE_20A_MULTI)
.EQU	MODE 	= 	2			; Choose mode. Set to 2 for multirotor
.INCLUDE "SuperSimple_20A.inc"	; Select SuperSimple 20A pinout
#endif

#if defined(SUPERSIMPLE_30A_MAIN)
.EQU	MODE 	= 	0			; Choose mode. Set to 0 for main motor
.INCLUDE "SuperSimple_30A.inc"	; Select SuperSimple 30A pinout
#endif

#if defined(SUPERSIMPLE_30A_TAIL)
.EQU	MODE 	= 	1			; Choose mode. Set to 1 for tail motor
.INCLUDE "SuperSimple_30A.inc"	; Select SuperSimple 30A pinout
#endif

#if defined(SUPERSIMPLE_30A_MULTI)
.EQU	MODE 	= 	2			; Choose mode. Set to 2 for multirotor
.INCLUDE "SuperSimple_30A.inc"	; Select SuperSimple 30A pinout
#endif
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

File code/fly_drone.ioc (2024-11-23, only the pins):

Mcu.UserName=STM32F103C8Tx
PA0-WKUP.Signal=ADCx_IN0
PA1.GPIO_Label=PIN_TEST
PA1.Signal=GPIO_Output
PA10.Signal=USART1_RX
PA13.Signal=SYS_JTMS-SWDIO
PA14.Signal=SYS_JTCK-SWCLK
PA3.Signal=S_TIM2_CH4
PA6.Signal=S_TIM3_CH1
PA7.Signal=S_TIM3_CH2
PA9.Signal=USART1_TX
PB0.Signal=S_TIM3_CH3
PB1.Signal=S_TIM3_CH4
PB10.Signal=I2C2_SCL
PB11.Signal=I2C2_SDA
PB3.Signal=SPI1_SCK
PB4.Signal=SPI1_MISO
PB5.Signal=SPI1_MOSI
PB6.GPIO_Label=SPI1_NSS
PB6.Signal=GPIO_Output
PB7.GPIO_Label=SI_SDN
PB7.Signal=GPIO_Output
PC13-TAMPER-RTC.GPIO_Label=PIN_TEST2
PC13-TAMPER-RTC.Signal=GPIO_Output

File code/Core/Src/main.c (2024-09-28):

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
/* Includes ------------------------------------------------------------------*/
#include "main.h"

/* USER CODE BEGIN Includes */

#include <string.h>		// for strlen
#include <stdio.h>		// for sprintf
#include <math.h>		  // for abs and other

#include "radio_config_Si4463.h"

// #include "debug.h"

#include "params.h"
#include "system.h"
#include "mavlink_handler.h"

#include "imu.h"

#include "ModemControl.h"
#include "MotorControl.h"
/* USER CODE END Includes */

ADC_HandleTypeDef hadc1;

I2C_HandleTypeDef hi2c2;

IWDG_HandleTypeDef hiwdg;

SPI_HandleTypeDef hspi1;

TIM_HandleTypeDef htim1;
TIM_HandleTypeDef htim2;
TIM_HandleTypeDef htim3;

UART_HandleTypeDef huart1;

void SystemClock_Config(void);
static void MX_GPIO_Init(void);
static void MX_ADC1_Init(void);
static void MX_I2C2_Init(void);
static void MX_IWDG_Init(void);
static void MX_SPI1_Init(void);
static void MX_TIM1_Init(void);
static void MX_TIM2_Init(void);
static void MX_TIM3_Init(void);
static void MX_USART1_UART_Init(void);
/* USER CODE BEGIN 0 */

void test_set(int set){
  if (set !=0) HAL_GPIO_WritePin(PIN_TEST_GPIO_Port, PIN_TEST_Pin, GPIO_PIN_SET);
  else HAL_GPIO_WritePin(PIN_TEST_GPIO_Port, PIN_TEST_Pin, GPIO_PIN_RESET);

}

volatile uint32_t tick_ms = 0;

uint32_t Get_tick(void){
  return tick_ms;
}

// void HAL_IncTick(void)
// {
//   uwTick += uwTickFreq;
// }

void SYS_myTick(void)  // IRQ 1 ms
{
  tick_ms++;
  //reset timer for calculate us
  if (htim1.Instance != 0)__HAL_TIM_SET_COUNTER(&htim1, 0); // reset for timer counter us
}

//void Printf(const char *fmt, ...){
//  HAL_UART_Transmit(&huart1, (unsigned char *)fmt, strlen(fmt), 500);
//}
#include <stdarg.h>
void Printf(const char *fmt, ...)
{
  char buf[256];
  va_list lst;
  va_start(lst, fmt);
  vsprintf(buf, fmt, lst);
  va_end(lst);
  HAL_UART_Transmit(&huart1, (unsigned char *)buf, strlen(buf), 500);
  if (ModemControl_getStatus()>=0) mavlink_send_statustext(buf);
}

// for printf. the size is larger on 2k
// int _write(int fd, char* ptr, int len) {
//     HAL_UART_Transmit(&huart1, (uint8_t *) ptr, len, HAL_MAX_DELAY);
//   ptr[len] = '\0';
//   if (ModemControl_getStatus()>=0) mavlink_send_statustext(ptr);
//     return len;
// }

/* USER CODE END 0 */

/**
  * @brief  The application entry point.
  * @retval int
  */
int main(void)
{

  /* MCU Configuration--------------------------------------------------------*/

  /* Reset of all peripherals, Initializes the Flash interface and the Systick. */
  HAL_Init();

  /* Configure the system clock */
  SystemClock_Config();

  /* Initialize all configured peripherals */
  MX_GPIO_Init();
  MX_ADC1_Init();
  MX_I2C2_Init();
  MX_IWDG_Init();
  MX_SPI1_Init();
  MX_TIM1_Init();
  MX_TIM2_Init();
  MX_TIM3_Init();
  MX_USART1_UART_Init();
  /* USER CODE BEGIN 2 */

  Printf("...\n\r");

  __enable_irq();
  HAL_IWDG_Init(&hiwdg);
  __HAL_IWDG_START(&hiwdg);
  HAL_IWDG_Refresh(&hiwdg);

  HAL_TIM_Base_Start(&htim1); // timer for us calculate
  HAL_TIM_Base_Start(&htim2); // reserv for additional motors
  HAL_TIM_Base_Start(&htim3); // timer for motor pwm

  HAL_TIM_PWM_Start(&htim2, TIM_CHANNEL_2); // for additional motors
  HAL_TIM_PWM_Start(&htim2, TIM_CHANNEL_4); // for additional motors

  HAL_TIM_PWM_Start(&htim3, TIM_CHANNEL_1); // motor 1
  HAL_TIM_PWM_Start(&htim3, TIM_CHANNEL_2); // motor 2
  HAL_TIM_PWM_Start(&htim3, TIM_CHANNEL_3); // motor 3
  HAL_TIM_PWM_Start(&htim3, TIM_CHANNEL_4); // motor 4

  params_restore();

  HAL_IWDG_Refresh(&hiwdg);

  MotorControl_init();

  if (imu_init() < 0) system_reboot();
  if (ModemControl_init() < 0) {Printf("MC_init false\n\r"); system_reboot();};

  Printf("Started...\n\r");

  /* USER CODE END 2 */

  /* Infinite loop */
  /* USER CODE BEGIN WHILE */
  while (1)
  {
    HAL_IWDG_Refresh(&hiwdg);

    int thread = Thread_Cycle();

    switch (thread){
        case(THREAD_IMU_LOOP):
          imu_loop();
          break;
        case(THREAD_TEST):
          // static int ii=0;
          // Printf("test %d\n\r", ii++);
          HAL_GPIO_TogglePin(PIN_TEST_GPIO_Port, PIN_TEST_Pin);
          if (MotorControl_isArmed()) system_changeThread(THREAD_TEST, THREAD_T_INTERVAL, 100);
          else system_changeThread(THREAD_TEST, THREAD_T_INTERVAL, 500);  //500

          // int alt_max = (int)params_GetParamValue(ALT_MAX);
          // if ((alt_max > 0) && (!MotorControl_isArmed())){
          //   int dist = imu_getAlt();
          //   Printf("dist = %d\n\r", dist);
          // }
          break;
        case(THREAD_MODEMCONTROL):
          mavlink_loop();
          if (ModemControl_Loop() == 1){  // if rx data pack
            uint8_t buff_pack[64];
            int32_t rx_len = ModemControl_GetPacket(buff_pack);
            mavlink_receive_pack(buff_pack, rx_len);  // send packet to parse
          }
          break;
        case(THREAD_MAV_SEND_ATTITUDE):
          mavlink_send_attitude();
          break;
        case(THREAD_MAV_SEND_STATUS):
          mavlink_send_heartbeat();
          mavlink_send_status();
          break;
        case(THREAD_ADC):
          Battery_Read();
          break;
    }

    /* USER CODE END WHILE */

    /* USER CODE BEGIN 3 */
  }
  /* USER CODE END 3 */
}

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


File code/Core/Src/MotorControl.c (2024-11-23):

/*

MotorControl_loop():
Example for PITCH Chan to M1:
/--------------------\  /---------------------\  /----------------------\
| Chan[PITCH]        |->| -PARAM_PID_P_OFFSET |->|*PARAM_PID_P_MUX_CHAN |
| from mavlink       |  | (-chan_p_offset)    |  | (*chan_p_mux)        |
|                    |  | /1000               |  |                      |
| Values:1000-2000   |  | OUT: -0.5...0.5 *   |  |                      |
\--------------------/  \---------------------/  \----------------------/
/---PWM------\  /---MOTOR-SETTINGS-----------------\              |
|            |  | PARAM_M1_ACTION  (m1_action)     |  /-----\     |   /----------\
|            |  | (m1_action set to +force[PITCH]) |  | PID |<----+--| IMU pitch  |
|            |<-| +PARAM_M1_OFFSET (m1_offset)     |  |     |         \----------/
|            |  | PARAM_M1_MIN     (m1_min)        |  \-----/         
|-ApplyMotor-|  | PARAM_M1_MAX     (m1_max)        |     |
\-Values()---/  \---SetMotorValues()---------------/   force[PITCH]

*- for throttle out values: 0..1

PARAM_P_MODE: 	bit 0		// Do not use angels from imu if set (pitch=0, rol=0...)
				bit 1		// If not set - reset motors, pids to default, when throttle equal 0 

*/


#include "stm32f1xx.h"
#include "main.h"
#include "MotorControl.h"
#include "mavlink_handler.h"
#include "params.h"
#include "imu.h"

void UpdateFromParam(void);

#define DECREASE_ANGLE(angel) {while (angel <-180) angel += 360.0f; while (angel>180) angel -= 360.0f;}

typedef struct {
	unsigned int throttle_p	:1;	// + throttle
	unsigned int throttle_m	:1; // - throttle
	unsigned int pitch_p	:1;
	unsigned int pitch_m	:1;

	unsigned int roll_p		:1;
	unsigned int roll_m		:1;
	unsigned int yaw_p		:1;
	unsigned int yaw_m		:1;
	
	unsigned int brashed	:1;	// set 1 when used all brashed motor. it is set PWM 0..MAX
	                            // set 0 when used servo or esc with 1..2ms impulse

} motor_action_struct;

typedef struct
{
	unsigned char Reset;
	float lastResult;
	float lastInput;
	float I;
	float P;
	float D;
	float MaxLimit;
} t_pid;

t_pid mPID[4] = {{1,0,0,0,0,0,1000.0f},
				{1,0,0,0,0,0,1000.0f},
				{1,0,0,0,0,0,1000.0f},
				{1,0,0,0,0,0,1000.0f}};

unsigned int motor_action[4];// = {0,0,0,0};
float motor_min[4];// = {0,0,0,0};
float motor_max[4];// = {1000,1000,1000,1000};
float motor_offset[4];// = {0,0,0,0};

float SetPID(volatile t_pid *PID, float input, float position);

static int armed = 0;
static int status = -1;

float motor[4];

void MotorControl_setArm(int a){
	armed = a;
}
int MotorControl_isArmed(void){
	return armed;
}
int MotorControl_getState(void){
	return status;
}
float MotorControl_getMotorValue(float * m){
	for (int i=0; i<4;i++) m[i] = motor[i];
	return 0;
}


int SetMotorValues(float throttle, float pitch, float roll, float yaw, float * m){
	for (int i=0;i<4;i++){
		float set_motor = 0;

		motor_action_struct * mAction = (motor_action_struct *) &motor_action[i];

		if (mAction->throttle_p) set_motor +=throttle;
		if (mAction->throttle_m) set_motor -=throttle;
		if (mAction->pitch_p) set_motor +=pitch;
		if (mAction->pitch_m) set_motor -=pitch;
		if (mAction->roll_p) set_motor +=roll;
		if (mAction->roll_m) set_motor -=roll;
		if (mAction->yaw_p) set_motor +=yaw;
		if (mAction->yaw_m) set_motor -=yaw;

		set_motor += motor_offset[i];

		if (set_motor > motor_max[i]) set_motor = motor_max[i];
		if (set_motor < motor_min[i]) set_motor = motor_min[i];

		m[i] = set_motor;
	}
	return 0;
}
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

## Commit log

2023-03-19 Filled in for a start
    [ESC_atmega8.kicad_pcb, ESC_atmega8.kicad_sch, stm32f103_FlyBoard.cfg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]
2024-02-17 added BL, corrected modem control
    [stm32f103_BL.cfg]
2024-05-31 after update cubemx
    [stm32f103_BL.cfg, stm32f103_FlyBoard.cfg, stm32f103_FlyBoard.kicad_pcb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]
2024-10-25 bootloader and main code in one folder. firmware address shifted to back
    [stm32f103_BL.cfg]

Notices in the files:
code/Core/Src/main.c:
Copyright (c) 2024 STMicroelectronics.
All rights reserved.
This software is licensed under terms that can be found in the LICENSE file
